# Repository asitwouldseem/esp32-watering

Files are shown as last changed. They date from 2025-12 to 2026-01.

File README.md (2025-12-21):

# esp32-watering
Project log for an ESP32 controlled watering system.

## Requirements
- Must be able to stand alone of Home Assistant. If HA goes offline for whatever reason, no plants should die! 
- Fault tolerant. Strive for professional, accept that I am merely a maker. 
- Ability to control water 'dosage' -- good plant parents know that watering shouldn't neccesarily be done on a schedule, and not all plants require watering consistently.
- Moisture sensors are out of scope. There are plenty of commercial solutions out there already. 
- Ability to detect when the storage tank runs dry and notify me.
- Packaged up in a neat, small profile package. No jiffy or (obviously) 3D printed jank. 
- Runs off USB-C. Probably 12V at this stage given the pumps and solenoids I'm seeing. 
- If possible, control from the ESP-32 D1 Mini form factor. I use a number of these prototyping boards already.
- Because I now have the "can design PCB" badge, assume order of 5 boards. Let's centralise as much as we can, but make the process reasonably repeatable if I want to run 2/3 zones down the track. 

## To Do
- Peristaltic pump to transfer the water from the tank to the plants
- Micro solenoids (NC) to control the flow to individual drippers (bonus points for daisy chained ones)
- Dripper heads + tube (preferably black)
- Float switch for water (simple circuit, only requires pull-down resistor)
- Container to store water
- Figure out pump flow rate -- we'll use this to set a default run time in ESPHome.
- Relays to control solenoid + pump. Could go with a H-bridge, but don't think we need PWM.
- Industrial design for box -- have seen cylindrical units.
- Most solenoids seem to run on 12V -- have plenty of sealed buck converters sitting around. Will break this out and have a 12V in and 5V in JST on the PCB.
- Will need a fuse, because maker paranoia.

More to follow!

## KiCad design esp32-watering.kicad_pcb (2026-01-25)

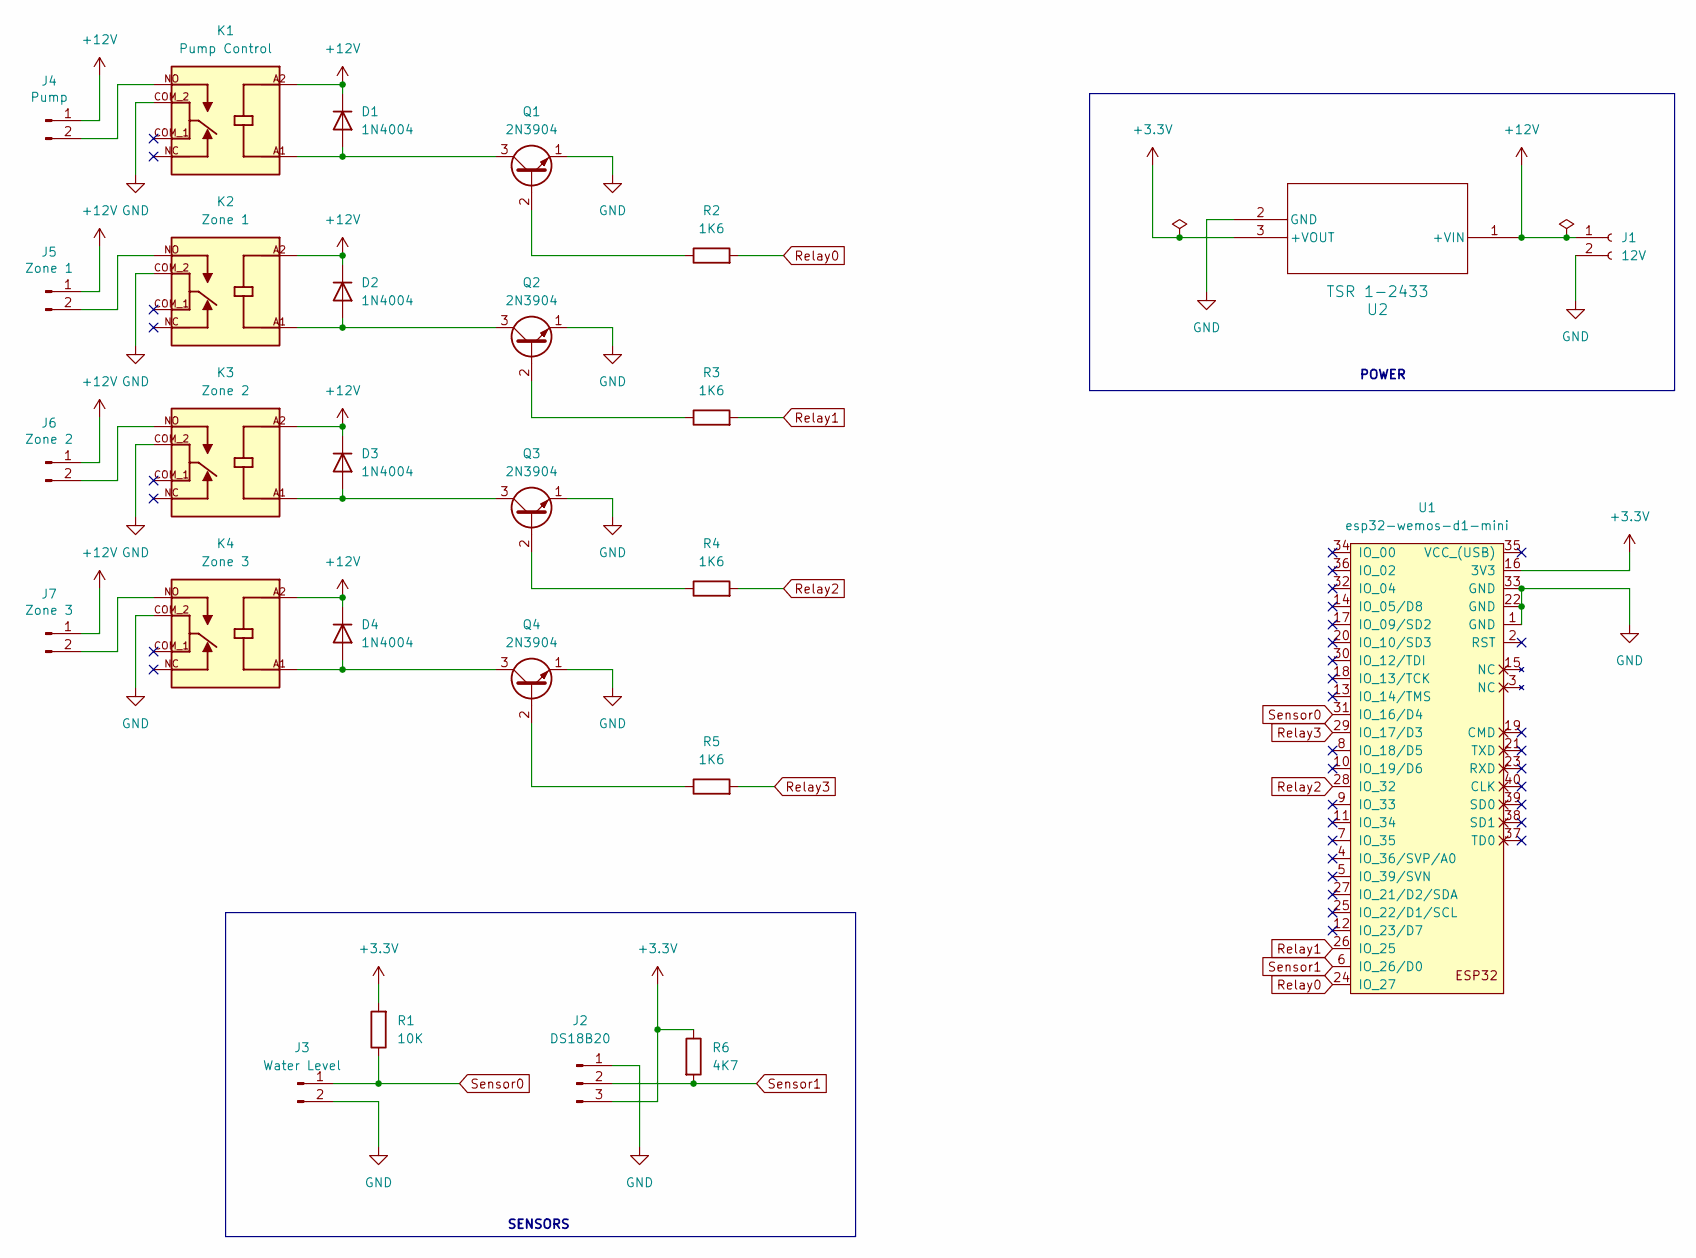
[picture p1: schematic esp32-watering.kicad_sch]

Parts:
D1, D2, D3, D4: 1N4004; D_DO-41_SOD81_P10.16mm_Horizontal
J1: 12V; JST_XH_B2B-XH-A_1x02_P2.50mm_Vertical
J2: DS18B20; JST_XH_B3B-XH-A_1x03_P2.50mm_Vertical
J3: Water Level; JST_XH_B2B-XH-A_1x02_P2.50mm_Vertical
J4: Pump; JST_XH_B2B-XH-A_1x02_P2.50mm_Vertical
J5: Zone 1; JST_XH_B2B-XH-A_1x02_P2.50mm_Vertical
J6: Zone 2; JST_XH_B2B-XH-A_1x02_P2.50mm_Vertical
J7: Zone 3; JST_XH_B2B-XH-A_1x02_P2.50mm_Vertical
K1: Pump Control; RELAY_SR5-12V-200-1C; PARTREV 1.01
K2: Zone 1; RELAY_SR5-12V-200-1C; PARTREV 1.01
K3: Zone 2; RELAY_SR5-12V-200-1C; PARTREV 1.01
K4: Zone 3; RELAY_SR5-12V-200-1C; PARTREV 1.01
Q1, Q2, Q3, Q4: 2N3904; TO-92_Inline
R1: 10K; R_Axial_DIN0204_L3.6mm_D1.6mm_P7.62mm_Horizontal
R2, R3, R4, R5: 1K6; R_Axial_DIN0204_L3.6mm_D1.6mm_P7.62mm_Horizontal
R6: 4K7; R_Axial_DIN0204_L3.6mm_D1.6mm_P7.62mm_Horizontal
U1: esp32-wemos-d1-mini
U2: TSR 1-2433; TSR1-SINGLE_TRP

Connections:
+3.3V: J2.3, R1.2, R6.1, U1.16 (3V3), U2.3 (+VOUT)
+12V: D1.1 (K), D2.1 (K), D3.1 (K), D4.1 (K), J1.1, J4.1, J5.1, J6.1, J7.1, K1.A2, K2.A2, K3.A2, K4.A2, U2.1 (+VIN)
GND: J1.2, J2.1, J3.2, K1.COM_2, K2.COM_2, K3.COM_2, K4.COM_2, Q1.1 (E), Q2.1 (E), Q3.1 (E), Q4.1 (E), U1.1 (GND), U1.22 (GND), U1.33 (GND), U2.2 (GND)
unnamed: D1.2 (A), K1.A1, Q1.3 (C)
unnamed: D2.2 (A), K2.A1, Q2.3 (C)
unnamed: D3.2 (A), K3.A1, Q3.3 (C)
unnamed: D4.2 (A), K4.A1, Q4.3 (C)
unnamed: J4.2, K1.NO
unnamed: J5.2, K2.NO
unnamed: J6.2, K3.NO
unnamed: J7.2, K4.NO
unnamed: Q1.2 (B), R2.1
unnamed: Q2.2 (B), R3.1
unnamed: Q3.2 (B), R4.1
unnamed: Q4.2 (B), R5.1
Relay0: R2.2, U1.24 (IO_27)
Relay1: R3.2, U1.26 (IO_25)
Relay2: R4.2, U1.28 (IO_32)
Relay3: R5.2, U1.29 (IO_17/D3)
Sensor0: J3.1, R1.1, U1.31 (IO_16/D4)
Sensor1: J2.2, R6.2, U1.6 (IO_26/D0)

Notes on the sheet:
POWER
SENSORS

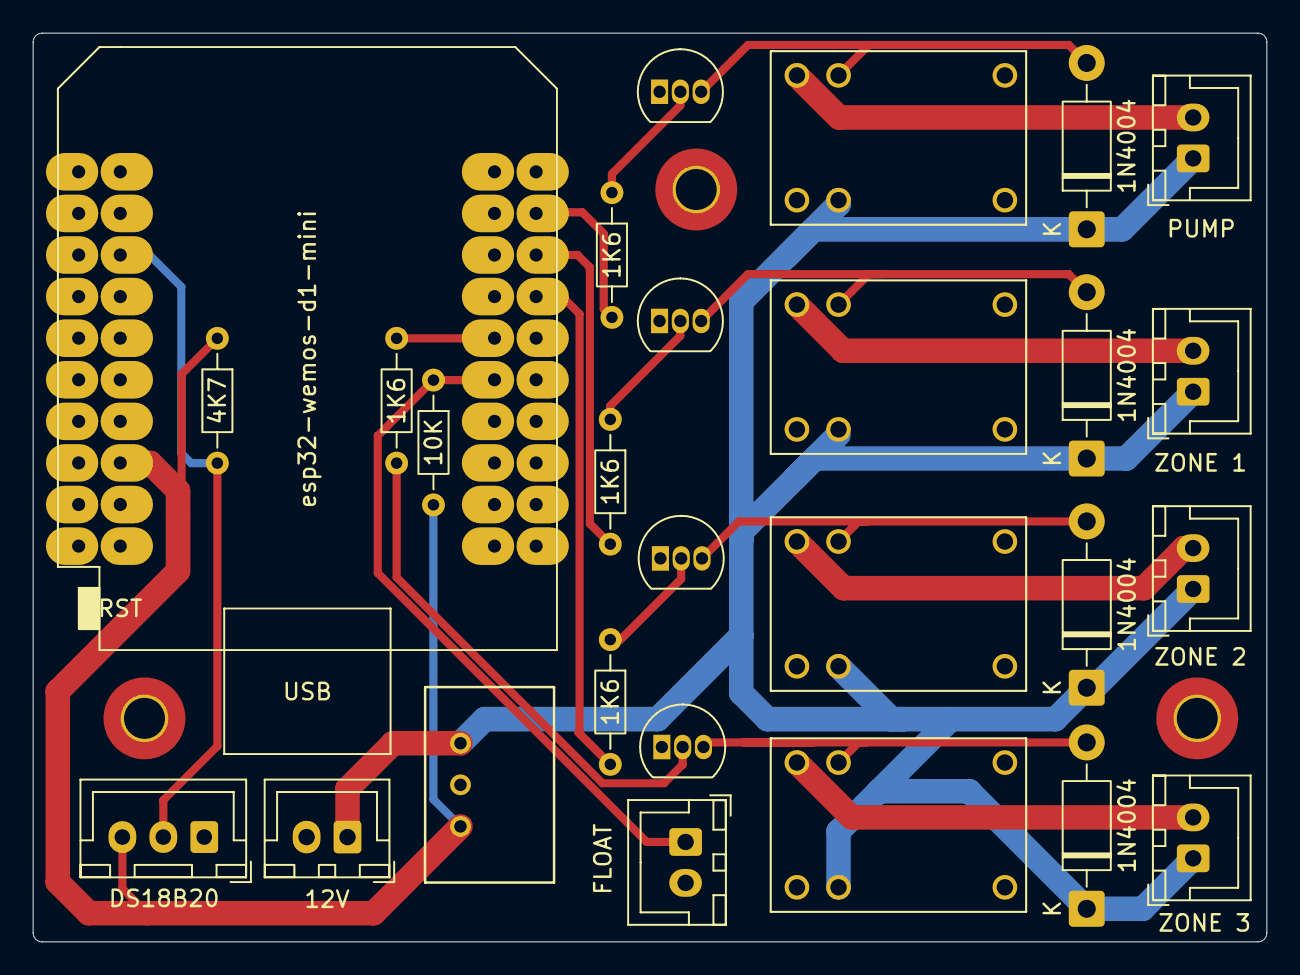
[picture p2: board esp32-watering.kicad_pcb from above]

Board: 2 copper layers, 75.3 x 55.5 mm, 27 parts (0 on the bottom side), 21 nets.

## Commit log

2025-12-21 Create KiCad Project
    [esp32-watering.kicad_pcb, esp32-watering.kicad_sch]
2025-12-21 Move out of directory
    [esp32-watering.kicad_pcb, esp32-watering.kicad_sch]
2025-12-21 Add relays and ESP32
    [esp32-watering.kicad_sch]
2025-12-21 Add pulldown resistor
    [esp32-watering.kicad_sch]
2025-12-22 First pass of schematic. Three zones.
    [esp32-watering.kicad_sch]
2025-12-22 Assign footprints
    [esp32-watering.kicad_pcb]
2025-12-22 Start layout
    [esp32-watering.kicad_pcb, esp32-watering.kicad_sch]
2025-12-22 More layout
    [esp32-watering.kicad_pcb]
2025-12-22 Indicative layout
    [esp32-watering.kicad_pcb]
2025-12-22 Initial layout
    [esp32-watering.kicad_pcb, esp32-watering.kicad_sch]
2025-12-22 Flip float valve
    [esp32-watering.kicad_pcb, esp32-watering.kicad_sch]
2025-12-23 Pass DRC
    [esp32-watering.kicad_pcb]
2025-12-23 Change silkscreen note
    [esp32-watering.kicad_pcb]
2025-12-24 Add rounded corners to PCB
    [esp32-watering.kicad_pcb]
2025-12-24 DFM Check
    [esp32-watering.kicad_pcb]
2025-12-27 Add Dallas sensor + decoupling cap
    [esp32-watering.kicad_sch]
2025-12-28 Add Traco 3.3V regulator
    [esp32-watering.kicad_pcb, esp32-watering.kicad_sch]
2025-12-28 Tidy ground plane
    [esp32-watering.kicad_pcb]
2025-12-28 Change silkscreen, refill zones
    [esp32-watering.kicad_pcb]
2025-12-28 Fix edge cut
    [esp32-watering.kicad_pcb]
2025-12-28 Join edge cuts DRC
    [esp32-watering.kicad_pcb]
2025-12-29 Remove ground pour under antenna
    [esp32-watering.kicad_pcb]
2025-12-29 V1.2 Change flyback diode location
    [esp32-watering.kicad_pcb]
2025-12-29 Align components, bump version
    [esp32-watering.kicad_pcb]
2025-12-29 Extend edge cut
    [esp32-watering.kicad_pcb]
2026-01-11 Submit to manufacture
    [esp32-watering.kicad_pcb, esp32-watering.kicad_sch]
2026-01-11 Create gerbers using toolkit
2026-01-11 Name nets
    [esp32-watering.kicad_sch]
2026-01-17 Bump version, add b.silkscreen for polarity
    [esp32-watering.kicad_pcb]
2026-01-25 Bump version, fix manufacturing error
    [esp32-watering.kicad_pcb, esp32-watering.kicad_sch]
2026-06-07 Bump KiCAD version
